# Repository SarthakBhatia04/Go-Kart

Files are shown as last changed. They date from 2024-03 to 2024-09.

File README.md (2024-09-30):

### Table of Contents
[Inspiration](#inspiration)   
[Brainstorming photos](#brainstrsoming-photos)  
[Component Research](#component-research)  
[Cad parts screenshots](#cad-parts-screenshots)     
[Process photos](#process-photos)  
[Errors and Solutions](#errors-and-solutions)  

Inspiration
=============
In the early stages of my go-kart project, I found a lot of inspiration by watching YouTube videos. I explored various channels where creators shared their builds, offering insights and tips that shaped my approach. Seeing others' innovative solutions and creative designs motivated me to experiment with different ideas and techniques. These videos not only provided technical guidance but also fueled my enthusiasm for the project, helping me visualize what was possible and encouraging me to push the boundaries of my design.

Brainstorming photos
=============





Component Research
=============
All of this went into a spreadsheet I made as I tracked the cost of the parts per item, amount needed, vendor, and schedule for when it would come.

## Wheels
- Spindle kit for the front two wheels
- 5/8th inch bolts for the back two wheels
- Wheels
- Spacers

With all this in mind, I started by searching on YouTube for spindle kits and came across a helpful video. I found a kit listed in the video description, which led me to notice that the bolts for the wheels were 5/8 inch. I wanted to use the same wheels for the rear, so I decided to get 5/8-inch screws for the back as well. I followed the recommendations from the YouTube description for the wheels, ensuring they would fit well with both the front wheels and the 5/8-inch rear bolts.

## Frame
- Aluminum/steel pipes

I found these steel pipes at Home Depot and there wasn't much research gone into this due to the fact I didn't want to order custom pipes.

## Steering wheels
- Standing bearers
- Pipe
- Wheel
- Laser-cut metals

## Engine
- engine
- laser cut engine holder

I tried to get a 78cc engine from Harbor Freight but it was unavailable to be shipped here so I ordered one from Harbor Freight which is 98cc and included a clutch and sprocket plus a chain. This helped as I didn't have to do trial and error in finding parts that find the engine like I would have done with the 78cc.

## Pedals and brakes
- pedals
- brake wires
- Brake drum

I got the brake drum from the same website I got the front axle from

Cad parts screenshots
=============
Note: Regarding Solidworks Parts and Assembly

The parts constructed in Solidworks are not up to scale. This discrepancy arises because most vendors do not give precise measurements of their components. The purpose of designing and constructing the parts and making the assembly is to visually display the functionality and relationship between the components. 

Price sheet is above in file name: Gokart Price sheet

## Assembly

## Pedal

## Frame pipe


This specific part was used a multitude of times but with edits to the length dimension
## Steering wheel

## Standing bearings

## Steering tie rods

## Wheel

## Wheel with the Brake drum


Many parts went into making this part, including spacers between the brake drum and the wheel split rim.
## Chair

## Steering wheel pipe

## Front axle connector



For this section, I had to create two separate parts because the right-side front axle faces the opposite direction compared to the left-side front axle. Instead of designing four distinct parts, I only needed to create two different parts and use one part for both sides, maintaining consistency and simplifying the design.

Process photos
=============
## Step 1


Organized the materials on the table. This is not a step that needea to be included but this helped me in order to check if I have all my materials to start a step. 
## Step 2


Measured how long the width and the length of the go-kart should be and marked them down with a Sharpie.
## Step 3


I cut the frame using an angle grinder. This was my first time using an angle grinder, so after cutting the pipes, I often had to use it again to straighten the tubes.
## Step 4


Put the cut frame in place to see if there were any measurements that were off.
## Step 5


Drilled L brackets in order to connect the tubes tgether and put them in place for welding activities and cold weld glue. This was a great help as i didn not have a designated welding setup with welding magnets that would the pipes together.
## Step 6


Put everything together the go-kart on the floor with what parts in their designated and started welding. I used black tape in order to hide my welds as my first time welds were not perfect. i alsoused the black tape to hide, cold weld glue residue.
## Step 7


The steering wheel I had listed on my Excel was too big with the outer rim and was 0.75 inches rather than 0.725 inches. With this being the case, I brought the bearings to a Home Depot and found another tube that would fit the bearings. The pipe was a little bigger than anticipated with a length of 3 feet rather than 2 feet, so I had to adjust the angle the steering wheel would rest to be a bit steeper. 
## Step 8


Since the bearings might fall or not be at the correct angle, and the supports might not be tall enough if installed at different times, I combined the steps of assembling the go-kart into one. First, I cut the support and glued the bearing to the front of the frame and the support area. This required multiple test trials. To ensure the angles were as close as possible, I used cold weld and secured it with tape after setting the cold weld. I believe this is sufficient, as welding would be difficult due to the bearing and tubes being made of different materials with different welding temperatures. Since I wanted a stable area to rest my feet near the pedals, I added a grill and let everything set with cold weld glue after welding. The same approach was applied here, as the grill and pipes were different materials, so I used little to no welding. Once everything was set, I installed the steering wheel and used tape to mark the approximate height I wanted the steering wheel to sit at by wrapping the tape around the area just above the bearing multiple times. This worked because the tape increased the pipe’s width at that point, preventing the steering wheel from sliding further down. This was a bit of an oversight, as welding a bearing would have looked better, but I chose tape in case I needed to adjust the steering wheel in the future. After that, I welded the tie rod connector to the frame and, as usual, cold welded and taped it afterward.
## Step 9


On the ground set up where the seat would go while also making sure there was room for the engine behind.
## Step 10


Attached the seat supports and attached the seats using screws I got from home depot.
## Step 11


Looking down below the seating area, I decided to pivot to help support the seating area so it wouldn't sag down within the area and give less stress to the go-karts' wheel areas.
## Step 12


Getting some shopping cart wheels and using some leftover pipes, I attached the wheels to two pipes and it was perfectly the exact height needed to be attached below the seat. I also made two more for the engine as I didn't want that much stress on the wheel next to engine which would be holdingthe brake drum as well. This of course will affect the steering of the go-kart but I decided the integrity of the go-kart was more important.
## Step 13


I attached the go-kart wheels and the engine supports with its own designated go-kart wheels. Also since the tie rods were too short, I made a home depot trip and got long screw rods that would fit the tie rod connectors. With that, I welded, cold-welded, and then taped the welding and glued mistakes on the steering wheels. Going back to step 8, I also had to untape the steering wheel to lower it further in order for the screw rods to fit.
## Step 14


The clutch and sprocket setup had different screw holes to attach it to the wheel, so i drilled new holes to make them match. After attaching the gear to the wheel, I put the engine on the go-kart to see where the correct place to put it and used a bike chain breaker and some pliers to break the chain. I then broight the correct size chain connector in ordertto connect the chain at the corrct lenght I wanted it at.
## Step 15


After marking where the engine should be I attached the engine mount to the go-kart
## Step 16



I attached the engine using some nuts and bolts I had got from Home Depot and then attached the pedal wires wrapping it with tape when itr was next to the chasis to secure a more tough and enhanced fit. Moving on, I used additional tubing, drilled holes in them for the pedals, and then attached the additional tubing to the go-kart so that the pedals would feel like they had more height for a bigger driver like myself. In order to attach the pedal wiring to the engine with greather ease, I removed a part of the engine using a bolt extractor set. The set I brought also came helpfule with filling up air in the tires as some tires needed reajusting before I could fill them with air. It also helped when i was attaching the  brake drum to the wheel.
## Step 17


Here is a picture of me sitting on it. Step 17 was just me having fun with the go-kart.

Errors and Solutions
=============

## Tie rods
- The tie rods were too short for the steering mechanism so I had to improvise and use only the connectors within the kit. I went to home depot and home screw rods where the screw would be all over the rod like with the steering wheel and used that instead. This warranted the steering wheel to be lowered also which in turn helped since the steering wheel being lowered made it in a more comfortable spot for reiders.

## Steering wheel
- The steering wheel I got had bad dimensions so I had to take the bearers and go around stores for a better fit. I eventually got a better fit with the problem being it was longer than what I had initially planned. Luckily with the tire rods also being longer than originally planned, the steering wheel was allowed to be lowered more which led to the height difference not being a big factor.

## Welding
- With this being my first tie welding, I was unable to make good welds and was also oblivious to the fact that aluminum and steel wouldn't weld well. So after I welded everything in place I used cold weld glue as well and also used black tape to hide all my welds and cold welding mistakes.

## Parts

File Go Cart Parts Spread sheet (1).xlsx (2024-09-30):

 | Part | Cost Per item | Quantity | Total item Cost | Vendor | Link | Schedule (#Days aprox.) | Product Identification ID
 | Seat | 20.7 | 1 | 20.7 | Walmart | https://www.walmart.com/ip/Go-Kart-Car-Seat-Go-Karts-Seat-Saddle-Adjustable-for-Racing-Cart-Durable-DIY/3644668507\ | 21-41 | B0C1G3X7N6
 | Steering wheel | 23 | 1 | 23 | Amazon | https://www.amazon.com/gp/product/B081DTSNTC?linkId=41368a7d85aba401ce068d8af1d5ce4a&language=en_US | 2 | B081DTSNTC
 | Pedals | 16.58 | 1 | 16.58 | Amazon | https://www.amazon.com/gp/product/B09YLY3Q1K?linkId=692ec461ab91f72f61d45bdb2f5b8991&language=en_US | 2 | B09YLY3Q1K
 | Spacers | 10.64 | 1 | 10.64 | Amazon | https://www.amazon.com/gp/product/B00NQR0UC2?linkId=d99ce064514770ba3342d6d5111db298&language=en_US | 1 | B00NQR0UC2
 | Standing bearings 20mm | 12.33 | 1 | 12.33 | Amazon | https://www.amazon.com/gp/product/B00YINI3RM?linkId=11ce0fb0649a8dd0c93fad268743cb00&language=en_US | 2 | B00YINI3RM
 | Steering pipes | 13 | 1 | 13 | Amazon | https://www.amazon.com/gp/product/B09P5835PJ?linkId=585bcb60b0fc0917032461f4a1eb0576&language=en_US | 1 | B09P5835PJ
 | Cables | 14.4 | 1 | 14.4 | Amazon | https://www.amazon.com/gp/product/B091DV78BL?linkId=7c71dc3a3a30c905685813211748111b&language=en_US | 1 | B091DV78BL
 | Clutch and chain | 27 | 1 | 27 | Amazon | https://www.amazon.com/gp/product/B08CVVHSWD?linkId=e266220a6c4dfaa1c7e905aba815d0b6&language=en_US | 1 | B08CVVHSWD
 | Hunter green spay paint | 3 | 1 | 3 | Amazon | https://www.amazon.com/Krylon-21205-9-Ounce-Spray-Hunter/dp/B005574DB0 | 3 | B005574DB0
Shipping + Tax |  |  |  | 17.23
 | 5/8th inch bolt | 6.16 | 2 | 12.32 | Home Depot | https://www.homedepot.com/p/Everbilt-5-8-in-11-x-8-in-Galvanized-Hex-Bolt-805776/204645589 (https://www.homedepot.com/b/Hardware-Fasteners-Bolts-Hex-Bolts/5-8-in/N-5yc1vZc2c0Z1z0sfy4) | 1 | 204645589
 | Flat metal sheet | 14.5 | 1 | 14.5 | Lowes | https://www.lowes.com/pd/IMPERIAL-24-in-x-3-ft-Galvanized-Steel-Sheet-Metal/3234805 (https://www.homedepot.com/p/Everbilt-24-in-x-48-in-Zinc-Plated-26-Gauge-Sheet-Metal-800567/204331375) | 1 | 204331375
 | Tubing 3/4'' | 14.89 | 1 | 14.89 | Home Depot | https://www.homedepot.com/p/STZ-3-4-in-x-2-ft-Black-Steel-Schedule-40-Cut-Pipe-306-34X24/100550442 | 1 | 100550442
 | Tubing 1x96'' | 31.18 | 3 | 93.54 | Home Depot | https://www.homedepot.com/p/Everbilt-72-in-x-1-in-x-1-1-16-in-Thick-Square-Tube-801127/204325635 (https://www.homedepot.com/p/M-D-Building-Products-1-in-x-96-in-Mill-Aluminum-0-063-in-Thick-Square-Tubing-59477/300185788) | 1 | 204325635
Shipping + Tax |  |  |  | 13.525
 | Throttle kit | 23.95 | 1 | 23.95 | Go Power Sports | https://www.gopowersports.com/throttle-kit-79cc-predator-engine/ | 2024-03-06 | 79CCTK
Shipping + Tax |  |  |  | 5.69
 | Spindle kit for breaking and steering | 51.95 | 1 | 51.95 | BMI Karts and Hobby shop | https://www.bmikarts.com/Complete-Spindle-Set--4-12-x-58-_p_1319.html | 3 | 421400
 | Drum brake and sprokets x4 | 23.9 | 1 | 23.9 | BMI Karts and Hobby shop | https://www.bmikarts.com/72T-35-Sprocket-5-1116-Bolt-Circle_p_11949.html | 3 | 774142
Shipping + Tax |  |  |  | 13.43
 | Tires | 10 | 4 | 40 | Vevor | https://www.harborfreight.com/heavy-duty-10-inch-groove-tread-tire-40729.html | 2024-01-04 | 69733
Shipping + Tax |  |  |  | 5
 | Engine | 102 | 1 | 102 | Harbor freights | https://www.harborfreight.com/generators-engines/engines/65-hp-212cc-ohv-horizontal-shaft-gas-engine-epacarb-69727.html (https://www.harborfreight.com/3-hp-79cc-ohv-horizontal-shaft-gas-engine-epa-69733.html) | Currently unavailable | 69733
Shipping + Tax |  |  |  | 20.31
 | Online laser cut chasis | 35 | 1 | 35 | TimWelds | https://timwelds.com/kart-laser-cut-files/ | 7 | None
Shipping + Tax |  |  |  | 5
Total Cost For Parts |  |  |  | 632.885
 | Welding Kit + Welding Sticks | 68+15 | 1 | 83 | Amazon | https://www.amazon.com/TOOLIOM-Machine-Inverter-Digital-Portable/dp/B08B3VHN54 | 1 | B08B3VHN54
 | Angle Grinder | 30 | 1 | 30 | Amazon | https://www.amazon.com/SKIL-9295-01-2-Inch-Angle-Grinder/dp/B0036WBGI4 | 1 | B0036WBGI4
 | Tape and L Brackets | 6 | 1 | 6 | Amazon | https://www.amazon.com/FATLODA-Stainless-Brackets-Furniture-1-57x1-57/dp/B0BLBWZYSQ | 1 | B0BLBWZYSQ
 | Nut and Wrench Kit | 20 | 1 | 20 | Amazon | https://www.amazon.com/REXBETI-Impact-Remover-Extractor-Storage/dp/B07W91Y3LQ | 1 | B07W91Y3LQ
Total Cost For Parts |  |  |  | 139
Total Cost For Everything |  |  |  | 771.885

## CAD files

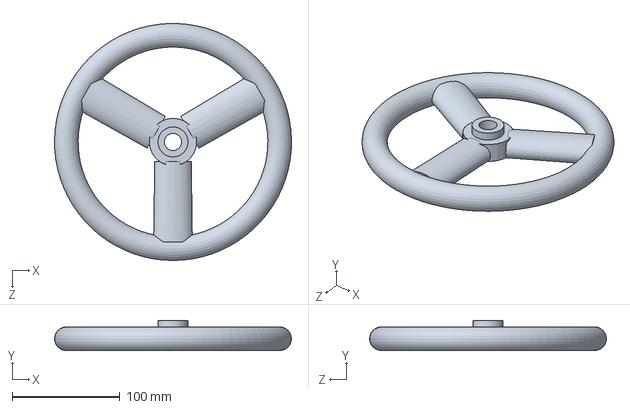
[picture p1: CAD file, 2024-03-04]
CAD_Files/steering wheel (1).SLDPRT
220.0 x 28.0 x 219.9 mm

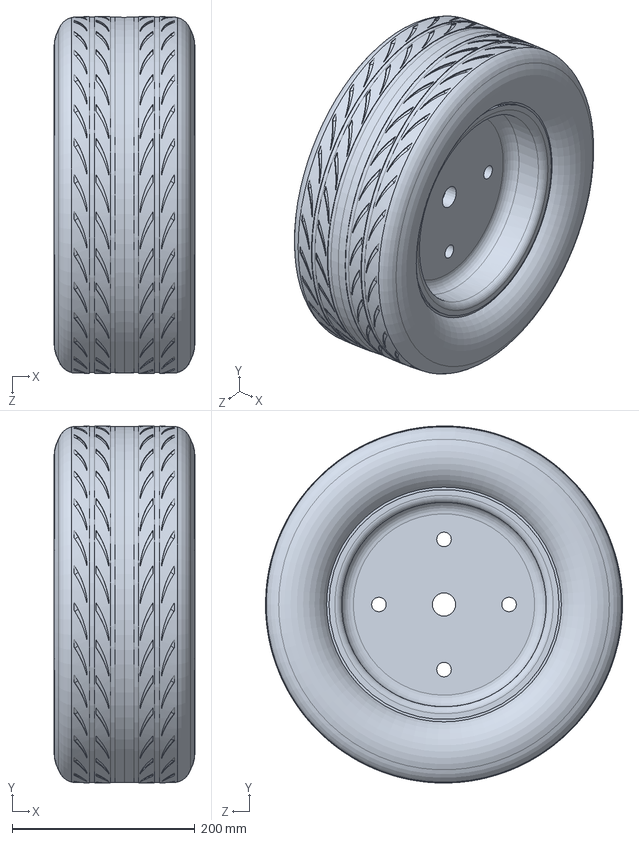
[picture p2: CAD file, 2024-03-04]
CAD_Files/tire with split rim (1).SLDPRT
153.9 x 390.2 x 390.2 mm

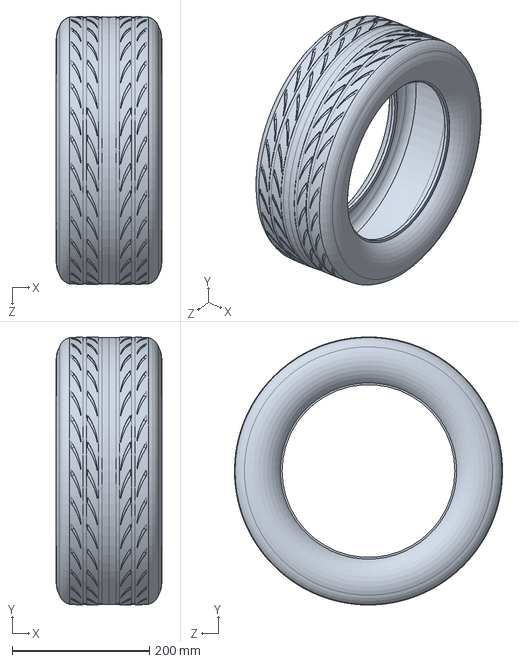
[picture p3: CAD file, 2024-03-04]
CAD_Files/tire (1).SLDPRT
153.9 x 390.2 x 390.2 mm

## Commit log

2024-09-04 Create Cad Files
2024-09-04 Rename Go Cart Parts Spread sheet.xlsx to Go-Cart-Parts-spreadsheet.xlsx
    [Go-Cart-Parts-spreadsheet.xlsx]
